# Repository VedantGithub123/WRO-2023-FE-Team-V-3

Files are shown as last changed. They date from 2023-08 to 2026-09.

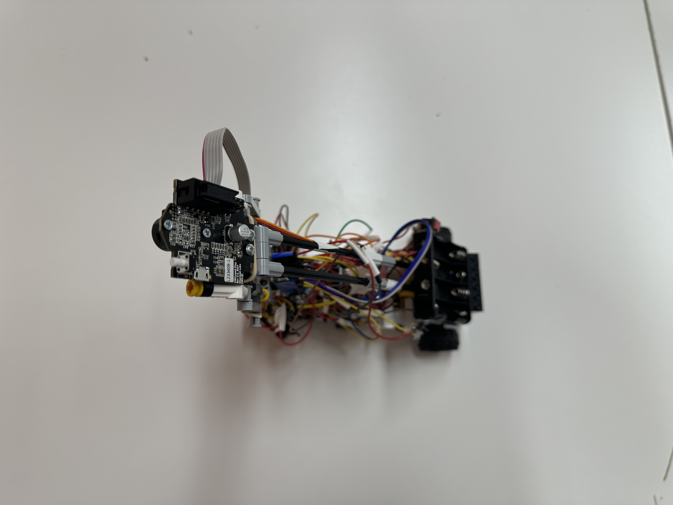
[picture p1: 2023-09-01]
photos/v-photos/v_top.jpg

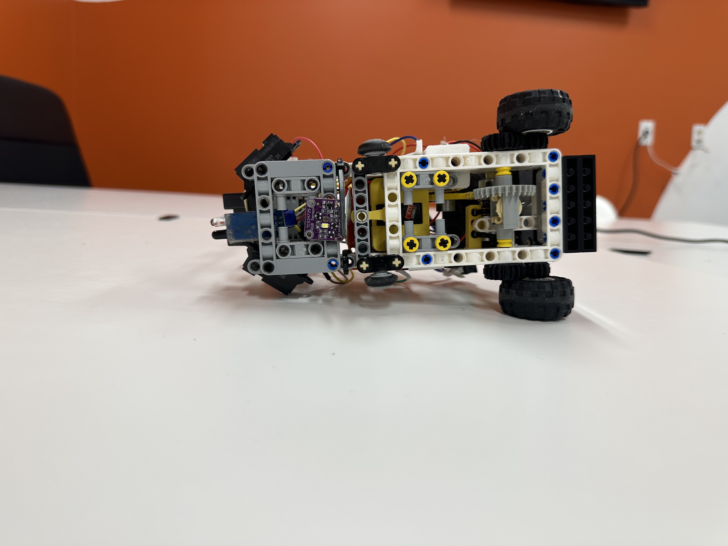
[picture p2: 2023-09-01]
photos/v-photos/v_bottom.jpg

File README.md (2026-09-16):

WRO Future Engineers Team V^3 Engineering Documentation
====

This repository contains engineering materials of a self-driven vehicle model participating in the WRO Future Engineers competition in the 2023 season. More information on each subcomponent of the robot is placed in the README.md files in each folder.

## Content
* `build` contains documentation about our chassis and material choice
* `electrical` contains schematic diagrams demonstrating the connections between different electromechanical components. It also includes the available datasheets for the aforementioned components, and it also has a markdown file explaining the reasoning for each component.
* `models` contains the files used by 3D printers to produce the vehicle elements.
* `photos` contains two folders where one contains the team photos and the other contains the robot photos
* `src` contains the code of control software for all components that were programmed to participate in the competition
* `strategy` contains documentation and diagrams explaining our approach to the problem
* `video` contains the video.md file with the link to a video where the driving demonstration exists

## Rubric Requirements
* `Mobility Management` is found in `build`, `electrical`, and `models`
* `Power and Sense Management` is found in `electrical`
* `Obstacle Management` is found in `strategy` and `src`
* `Pictures - Team and Vehicle` is found in `photos`
* `Performance Videos` is found in `video`
* `Engineering Factor` is found in `build` and `README`

### Who We Are
Team V^3 is an aspiring group of high school and university students who aim to be leaders in the future of autonomous vehicles. By taking the initiative to take part in the WRO Future Engineers challenge, we hope to gain experience in this field of engineering and problem-solving. We have been exposed to many robotic and logical challenges through Zebra Robotics, where we participated in many problems, such as WRO Robomissions, FIRST LEGO League, and VEX Robotics Competition. Our goals for this season are the following:
- Gain knowledge in the field of autonomous vehicles
- Expose ourselves to the nuances of software organization (i.e. Github)
- Become proficient in the skills regarding electronic components
- Learn how to coordinate and work as a team to solve the problem with innovation and creativity

### Our Robot & Iterations
Our team has designed a four-wheel rear-driver autonomous vehicle to complete the 2023 WRO Future Engineers challenge. When making our robot, we wanted to be able to rapidly iterate and make changes whenever they were needed. To accomplish this, our chassis and frame are almost entirely made of LEGO Technic parts and any remaining additions and part adapters (i.e., motor adapters, sensors, etc.) were designed on SolidWorks and Fusion 360 CAD Software and were printed using PLA filament on Anycubic Kobra 3D printers. Our current robot is a small and compact vehicle causing it to be highly maneuverable, allowing us to avoid obstacles effortlessly. This vehicle is powered by 300rpm 6V Micro Gear Box DC motors, allowing us to keep a compact and lightweight robot. To steer this chassis, we are using the ES08MA Metal Analog Servo, which has an ample amount of torque and strength. This allows us to make sharp turns whenever needed.
Prior to making this robot, our team went through various different iterations and prototypes where we learnt many lessons about what our optimal robot should consist of. These lessons are the following:
- Be small and compact
- Effectively use sensors to identify our location and our ideal path
- Speed is not the first priority for this challenges
- Maneuverability is key to solving the obstacle challenge

One of these was a larger robot with the usage of many more sensors and parts. However, its large nature at 30x20x30cm caused it to be difficult to maneuver and control. All of our efforts were in vain as we faced many hardships and problems when trying to program that robot. Our robot’s turning radius was too large, and it was unable to maneuver around the obstacles while our sensors were placed inconveniently and were unable to correctly and quickly construct an efficient path for our robot to take. We realized that many parts of our robot were unnecessary, especially the sheer size of it, and we ultimately decided to do a complete redesign which led to our final robot design. A summary of the reasons for our redesign can be found below:

| | Pros | Cons |
| - | ---| ---|
| Old Robot | <ul><li>Allows for the attachment of larger sensors</li><li>Faster robot due to the larger, more powerful motors</li></ul> | <ul><li>Bad maneuverability due to size, causing a larger turning radius</li><li>Excessive use of unnecessary sensors</li><li>Not enough ports due to the sheer number of sensors</li></ul> |
| New Robot | <ul><li>Smaller and more compact</li><li>Better maneuverability and sharper turning radius</li><li>More effective use of sensors and gets rid of any unnecessary parts</li></ul> | <ul><li>Slower speed due to less powerful motors</li><li>Restrictions to the size of sensors and parts we can use</li></ul> |

| Old Robot | New Robot |
| --- | --- |
|  |  |

### Electrical Components
Our chassis is controlled by the Arduino Nano microcontroller, which gets information from various sensors and uses said information to control the motors using an L298N motor controller board. The sensors that we are using for our vehicle are the following:
- Pixycam 2.1
- TCS34725 RGB Sensor

- HW-201 IR Sensors
- GP2Y0A02YK0F IR Range Sensor
- L3G4200D 3-Axis Gyro

We use the Pixycam 2.1 to identify the locations of the obstacles and effectively avoid them. The TCS34725 RGB sensor tells the microcontroller when it reaches a corner. Both IR sensors are used to detect the walls on the side and on the front. Finally, we use the L3G4200D gyro to know which direction we are facing. More information about our robot’s electrical components can be found in the README file in the electrical folder.

### Strategy and Code
For the open challenge, our sensors are strategically placed in ways that allow us to detect walls at a 45° or less angle. This allows us to adjust accurately based on the distance from the wall, ultimately providing an optimal path to solve this challenge. In order to measure the number of laps we do, we use the RGB sensor to count the number of lines passed and then our robot stops after some time once 12 lines have been measured. This is implemented in the code by using the following lines:
```
if (cornerCount==12)
{
  endTime = millis()+5000;
}
```

The cornerCount variable keeps track of how many corners the robot has passed during its run. The number is twelve as the square-shaped mat has 4 corners, and the robot must complete three laps.
We have two strategies for the obstacle challenge. The first of which only focuses on one block at a time and avoids it. The other strategy involves planning a route for each stretch of the lap and getting the robot to follow that path. Some code for the first challenge is the following:

```
if (closeBlock.m_signature==1)
{
  target = (207-closeBlock.m_y)/1.3-15;
}
else
{
  target = 315.0-(207-closeBlock.m_y)/1.3+15;
}
err = -150.0*(closeBlock.m_x-target);
```

This code gets the closest block and sets the target position of that block onto either side of the robot based on the color of the block.

All in all, this robot is a testament to our team’s adaptability and problem-solving skills, as we were able to completely redesign and program a new and more compact robot after learning from our previous mistakes. We hope that this robot and our hard work will lead us to success, and we look forward to competing!

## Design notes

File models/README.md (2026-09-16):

Models
====

This directory contains all the models used for our robot. Since our robot is made out of LEGO technic pieces, we are going to be 3d printing mounts and adapters for the electronics. Below is a table of our 3D-printed parts and what they are used for.

| File Name | Description | Image |
| --- | --- | --- |
| gear.stl | To solve the problem of transferring the power from the 6V motors to the LEGO axles, we designed and 3D printed a gear that is mounted on the motor's shaft and meshes with the LEGO differential. We had to create our own gear because the motors have a 3mm D-shaped insert which differs from a plus-shaped LEGO axle. |  |
| motor-mount.stl | With motor stability being a crucial part of our drivetrain, we needed to create our own mount to properly secure the motors to our chassis. This helps with our robot's balance and evens out the centre of gravity by allowing us to place one motor on opposite sides. |  |
| motor-bracket.stl | This piece has similar functionality to our motor mounts, except it required a different shape due to where it was placed in our robot. |  |
| servo-adapter.stl | Similar to the motor adapter, our servo motor's power must also be transferred to LEGO pieces. As a result, we created a matching axle slot, which we tuned by prototyping with different dimensions, and a slot for the servo motor, which we also adjusted by creating multiple iterations. |  |
| servo-mount.stl | Our servo motor needed to be secure in order to have crisp steering and minimal unwanted movement. To achieve this, we modelled a mount for the servo motor that would attach to our chassis and also contain a slot that perfectly fits the servo motor. |  |

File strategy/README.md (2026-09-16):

Strategy
====

This directory consists of an explanation and diagrams of our strategy for both the open and obstacle rounds.

## Open Challenge Strategy

In the open challenge, the only changes to the field are the size of the interior walls. In order to combat these changes, we will be using IR distance sensors to identify the distance from the walls. By having multiple distance sensors, the robot can accurately calculate the distance to the surrounding walls. The robot can use these sensor readings to correct itself and make sure it goes parallel to the wall. The robot will know when to turn due to the usage of a RGB sensor which detects the colored lines in the corner. This will also allow us to keep track of the number of laps we complete so we know when to end. Below are diagrams and flow charts demonstrating the process.
| Straight Movement | Turning |
| --- | --- |
|  |  |

| Open Challenge Flowchart |
| ------------------------ |
|  |

## Obstacle Challenge Strategy

For the obstacle challenge, we have two strategies for approaching the problem. The first one is to only consider the first obstacle and act according to that, while the other is to plan a path for one side of the round and follow that. We are working with both strategies and testing both simultaneously to determine the better strategy. To detect the obstacles, we are using the Pixycam 2.1, which gives a list of objects to the Arduino Nano.

### Strategy 1

The first strategy to approach the obstacle challenge is to keep the closest color on the corresponding side of the robot. This is implemented by getting the x-position of the object on the camera and accordingly changing the steering to make sure the object is on the correct side. The turning and stopping will use the same logic as the open challenge. In order to know how much to steer when we see the object, we will use a proportional control loop to ensure that our movements are efficient.

| Obstacle Challenge Simple Approach |
| ---------------------------------- |
|  |

### Strategy 2

Our second strategy for the obstacle challenge is to plan a path for each stretch of the mat and get the robot to follow that path. By having the current position, current heading, target position, and target heading, we can generate a polynomial to fit these parameters. We do this with multiple target points to create a target path which we aim to follow and steer the robot so it aims to move in the direction of the next point. This path takes into account the position of the obstacles and maps points that avoid them. We then repeat this process until the three rounds are over. 

| Obstacle Challenge Complicated Approach |
| ---------------------------------- |
|  |

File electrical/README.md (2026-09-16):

Electrical
====

This directory consists of schematic diagrams demonstrating the connections between different components as well as datasheets for the components. It also consists of the reasoning behind the choice of components.

## Parts Explanation

| Part Name | Explanation | Image | Datasheet |
| --- | --- | --- | --- |
| 1.5V Rechargeable Lithium Ion Battery | We are using this battery to power all of our electronics as it is compact and easy to get. They are also efficient for us as they are rechargeable and do not have to be replaced. |  |  |
| DC 6V Micro Gear Box Speed Reduction Motor, 300RPM | We are using this specific motor to drive the robot as it contains a gearbox that can reach a maximum speed of 300RPM. The compact size of these motors, coupled with a high RPM, allowed for our smaller compact design to succeed. |  |  |
| CJMCU34725 TCS34725 RGB Light Color Sensor | Using this RGB color sensor allows our robot to sense the blue and orange lines at the corners of the mat. This allows us to keep track of how many laps the robot has completed and indicate when the robot needs to turn. |  | [Color Sensor Info](https://www.waveshare.com/w/upload/b/bb/TCS34725_Color_Sensor_user_manual_en.pdf) |
| Arduino Nano | In order to process the information from the sensors and make decisions based on the running code, we are using the Arduino Nano, which is programmed with the Arduino IDE. This board is easy to use, and there are many libraries available and on demand. The board contains 14 digital input/output pins, enabling us to connect a multitude of devices. It also has eight analog pins, of which two are used for I2C communication. |  | [Arduino Nano Info](https://www.arduino.cc/en/uploads/Main/ArduinoNanoManual23.pdf) |
| ES08MA Metal Analog Servo | In order to steer our vehicle, we use a servo motor with 2.0 Kilogram-force centimetres of torque and a speed of 0.10 sec/60°. Since steering will require a reasonably large amount of torque, this motor provides more than enough for our application. Furthermore, this servo motor can turn quickly, which allows us to make incredibly sharp turns. |  | [Servo Info](https://m.media-amazon.com/images/I/61ZU3A84tYS._AC_SL1000_.jpg) |
| GP2Y0A02YK0F IR Range Sensor | The IR sensors provide the necessary information on the distance to the walls at an extremely fast rate. These specific sensors sense distance accurately from 20 to 150cm. We use one of these sensors to detect how close we are to any wall in front of our robot. We use the other two to follow the wall to make sure or robot is in the middle of the track |  | [GP2Y0A02YK0F IR Range Sensor Info](https://cdn.robotshop.com/media/d/dem/rb-dem-02/pdf/datasheet-gp2y0a02yk0f.pdf) |
| GP2Y0A41SK0F IR Range Sensor | We use these sensors to measure the distance to any walls on the sides of our robot. Since we need sensors with a smaller range to detect when we are getting close to the wall, we are using these ones. |  | [GP2Y0A41SK0F IR Sensor Info](https://www.pololu.com/file/0J713/GP2Y0A41SK0F.pdf) |
| HW-201 IR Sensor | In order to detect if our robot is going to crash into any object in the front, we use these sensors as a fail-safe to make sure our robot will still work. |  | [HW-201 IR Sensor Info](https://www.circuits-diy.com/hw201-infrared-ir-sensor-module/) |
| L298N Dual H-Bridge Motor Driver | To effectively power our motors, we are using the L298N motor driver, where we are able to control the direction and speed of both motors using Pulse Width Modulation (PWM). |  | [Motor Driver Info](http://www.handsontec.com/dataspecs/L298N%20Motor%20Driver.pdf) |
| L3G4200D Triple Axis Gyro Angular Velocity Sensor Module | We use a gyro angular velocity sensor to determine our vehicle's angular direction and accurately measure the change in angle per turn. To get accurate angle measurements from the gyro, we integrate the yaw angular velocity after calibrating the gyro to determine the robot's angle relative to its starting position.  |  | [Gyro Info](https://www.elecrow.com/download/L3G4200_AN3393.pdf) |
| PixyCam Pixy 2.1 Robot Vision Image Sensor | Since the Arduino Nano does not have enough computing power to process images, we are outsourcing the processing to the Pixy 2.1. This camera is able to provide the microcontroller with the necessary information to plan an appropriate path for the robot to take. |  | [Pixy 2.1 Info](https://docs.pixycam.com/wiki/doku.php?id=wiki:v2:start) |

## Parts Bill Of Materials (BOM)
| Part Name | Quantity |
| ---| --- |
| 1.5V Rechargeable Lithium Ion Battery | 4 |
| DC 6V Micro Gear Box Speed Reduction Motor, 300RPM | 2 |
| CJMCU34725 TCS34725 RGB Light Color Sensor | 1 |
| Arduino Nano | 1 |
| ES08MA Metal Analog Servo | 1 |
| GP2Y0A02YK0F IR Range Sensor | 3 |
| GP2Y0A41SK0F IR Range Sensor | 2 |
| HW-201 IR Sensor | 1 |
| L298N Dual H-Bridge Motor Driver | 1 |
| L3G4200D Triple Axis Gyro Angular Velocity Sensor Module | 1 |
| PixyCam Pixy 2.1 Robot Vision Image Sensor | 1 |

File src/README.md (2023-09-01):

Control software
====

This directory contains the code required for our robot and explains it

## Software and Language
To program our robot, we use the Arduino IDE and code an Arduino Sketch based on C++. Compiling and uploading our code is a simple process, as there are two buttons to help verify and upload our code. The click of this button will automatically compile and upload our code to the Arduino Nano microcontroller.

## Organization of Code
Our code follows Object-Oriented Programming (OOP) conventions, where we utilize classes for each and every one of our robot's sensors and components. The libraries that we are using to interface with our electronic components are:
Servo.h (For controlling the servo motor)
Adafruit_TCS34725.h (For reading the RGB sensor)
Adafruit_Sensor.h (For reading the gyro sensor)
Wire.h (For reading the gyro sensor)
Pixy2.h (For reading the Pixy camera)
### Chassis Class
In the chassis class, five-member variables are utilized to control the driving motors and the steering. These variables are "enA", which is used to store the pin that is connected to the enable port on the motor controller, and "in1" and "in2", which are used to store the pins connected to the inputs on the motor controller. We also use "sPort," which holds the pin connected to the micro servo. Finally, we have a steering variable, an instance of the steering class imported from the Servo.h library, which is used to control the micro servo we are using.

The constructor for this class takes in four inputs which are the ports used for the chassis, as mentioned above. These inputs are then stored in the member variables for later use in the class instance. 

The first method in our class is the move function which takes in an integer speed and limits it from -255 to 255. It then goes through some logic determining which inputs to turn on or off to drive in the right direction. In the following code, we check if the speed is zero, positive, or negative and set the input pins accordingly.
`if (speed == 0) { digitalWrite(in1, LOW); digitalWrite(in2, LOW); } else if (speed > 0) { digitalWrite(in1, HIGH); digitalWrite(in2, LOW); } else { digitalWrite(in1, LOW); digitalWrite(in2, HIGH); }`

The second method in our class is the steer function which steers our servo motor to the right angle. This method limits an angle variable to a specific range and then writes that range to the servo motor's input pin. The following code limits the range to -70 to 70, adding 94 as an offset.
`steering.write(angle / abs(angle) * min(abs(angle), 70) + 94);`

The third and final method in our class attaches the servo port to the instance of the Servo class defined in the chassis class. This is done by implementing the following code.
`steering.attach(sPort);`

### rgbSensor Class
The rgbSensor class interfaces with the TCS34725 RGB sensor using I2C (Inter-Integrated Circuit) communication to get the RGB values from the sensor. This class has one member variable, the "Adafruit_TCS34725 tcs", which controls the RGB sensor.

The first method in this class is the "getColor" function which returns the detected colour. The following code gets the RGB values and sets the corresponding variable to the values. `tcs.getRGB(&red, &green, &blue);` We then check the blue and red values to determine if the sensor is seeing blue, orange, or white in the following code. `if (blue > 90 && red < 60) { col = 2; } if (red > 80 && blue < 60) { col = 1; }`

The second method in this class is the "setup" function, which starts the TCS34725 sensor.

### IRSensors Class
This class is used to interface with the IR sensors that we are using. The member variables in this class are "int irPorts[4]" which is an array of four ports that hold the ports the sensors are connected to.

The constructor of this class takes in an array as input and assigns the values of the array to the irPorts array.

The first method of the class is the "getDistance" function which returns values based on which sensor it is using. If the sensor is the one in the front used for sensing long distances, we map the voltage to a function that returns the length. This function is implemented in the following code. `return (11.63417 + (241.6444 - 11.63417)/pow((1 + (analogRead(irPorts[port])*5.0/1023.0/0.5075672)), 1.868922))*1.5;` If the sensor is the one in the front and is used for short distances, we return one if it senses something and zero if not. Finally, if none of those are done, we return one if the sensor output voltage is larger than 0.93V and 0 if not.

The second method in this class is the "getDistanceClose" function which acts the same as the "getDistance" function but only returns one for the default case if the voltage is larger than 3.4V.

The third method in this class is the "getFarDistance" function which maps the voltage read from the IR sensor to a function to return the distance seen. This is done with the following code. `return ((138.672)/pow(1.0 + 5.56591*(analogRead(irPorts[port])/200.0), 1.24888)) + (-0.0340614 * pow(analogRead(irPorts[port])/200.0, 3));`

The final function in this class is the setup function which sets the pin modes for all the ports.

### Gyro Class
The Gyro class is used to interface with the L3G4200D gyro sensor through I2C communication. This class has four member variables which are the "angle", "prevTime", "drift", and "L3G4200D_Address".

The first method of the class is the "setup" function which writes to the gyro registers to set it up for use. This is done in the following code. `writeRegister(L3G4200D_Address, CTRL_REG1, 0b00001111); writeRegister(L3G4200D_Address, CTRL_REG2, 0b00000000); writeRegister(L3G4200D_Address, CTRL_REG3, 0b00001000); writeRegister(L3G4200D_Address, CTRL_REG4, 0b00110000); writeRegister(L3G4200D_Address, CTRL_REG5, 0b00000000);`

The second method is the "writeRegister" function which utilizes the "Wire.h" library to write to a particular address.

The third method is the "readRegister" function which also utilizes the "Wire.h" library to read information from a particular address.

The fourth method is the "getGyroChange" function which gets the angular velocity of the gyro. This is done by using the "readRegister" function and shifting the bits to get the value as shown in the following code. ` return ((zMSB << 8) | zLSB);`

The fifth method in the Gyro class is the "getAngle" function which returns the robot's angle by returning the "angle" variable stored in the Gyro class.

The sixth method in the Gyro class is the calibrate function which takes 6000 sample inputs and finds the average. This is the drift of the gyro, which we store in the drift variable for later use. We do the calibration with the following code. `for (int i = 0; i < 6000; i++){ drift +=getGyroChange(); } drift /= 6000; prevTime = micros();`

The final function in the class is the "updateGyro" function which updates the angle of the gyro when called. It does this by multiplying the value of the gyro by the time since the last call and then by a constant and adding that to the angle variable. This is done in the following code. `angle += (micros() - prevTime) / 1000000.0 * (getGyroChange() - drift) / -14.286 * 9/8 * 90/95; prevTime = micros();`

### Camera Class
The Camera class interfaces with the PixyCam 2.1 through SPI (Serial Peripheral Interface) and gets the detected blocks. The member variable in this function is the "pixy" variable, an instance of the Pixy2 class provided by the "Pixy2.h" library. 

The first method in the class is the "setup" function which initializes the PixyCam 2.1. This is done by using the "pixy.init()" function provided in the library.

The second method in the Camera class is the "getClosest" function which returns the closest signature to the robot. The PixyCam 2.1 has the closest signature as the first element in the array of blocks, so we return that first signature as shown in the following code `pixy.ccc.getBlocks(); return pixy.ccc.blocks[0];`

The final method in the class is the "getClosestBlock" function which gets the closest signature which is green or red. This is done to ensure that we do not return the line. We do this by going through the array of blocks, and if the signature is less than or equal to two, we return that block.

## Setup Code
In the setup of our program, we have a multitude of global functions and variables that we use in our main program. 

Arduino requires us to have a `void setup()` function, which runs once when the Arduino is turned on and a `void loop` function, which runs repeatedly until the Arduino turns off. In our code, we keep the setup of all the sensors and then wait until the button is pressed in the `setup` function, and we use the `loop` function to run our code. The first function that we use in our code is the `void delay_2` function which takes in an integer value and delays for that amount of milliseconds while updating the gyro sensor. We use this function instead of the default `delay` function since it allows our gyro sensor to constantly update. We then have two separate functions for each challenge. The `void open` function contains the code for the open challenge, and the `void obstacle` contains the code for the obstacle challenge. We implement these functions in the `loop` function by commenting on which function we are not running and uncommenting the function that we are running.

The global variables that we have in our code are the following
| Variable Name | Type | Purpose |
| --- | ---- | --- |
| chassis | Chassis | Creates an instance of the Chassis class for movement |
| rgbSense | rgbSensor | Creates an instance of the rgbSensor class for sensing lines |
| irPorts | int[4] | Stores the values of the IR sensors' ports |
| irSensors | IRSensors | Creates an instance of the IRSensors class to use the IR sensors |
| gyro | Gyro | Creates an instance of the Gyro class to measure the robot's angle |
| camera | Camera | Creates an instance of the Camera class to detect obstacles |
| buttonPort | int | Stores the port of the button |
| speed | int | Defines the speed for the robot and is used for acceleration |
| cornerCount | int | Stores the number of corners passed |
| endTime | unsigned long int | Stores the time when our robot should stop moving |
| dir | int | Stores the direction of the lap |
| cornerScanDelay | unsigned long int | Stores the time a corner was passed |
| cornerDetected | bool | Stores if a line has been detected |
| steer | float | Stores the steering value |
| prevObj | Block | Stores the previous block |
| closeBlock | Block | Stores the closest block |
| target | int | stores the target position for the blocks |
| err | float | Stores the error for following |
| kP | float | Stores the kP value for following |
| objDelay | int | Stores the time when an object is passed |
| targetAngle | int | Stores the target angle for gyro following |
| caughtOnWall | bool | Used to detect when to wall follow |

## Open Challenge Code
In the open challenge, we implement gyro and IR following, which uses readings from the sensors to ensure a straight path. Before we pass the first corner, the robot does not know which direction it is travelling in, so it gyro follows. We implement gyro following in the following code where it finds the difference between the target angle and the current angle and multiplies that error to get the steering. `err = targetAngle - gyro.getAngle(); steer = err*2.0;` To set our direction, we run this code constantly which checks if the direction is not set, it will reset it to whatever the RGB sensor is seeing. `if (dir==0) { dir = rgbSense.getColor(); }` The next part of our code checks if the RGB sensor sees the same color as the direction that the robot is travelling and it has been 2 seconds since the last line was seen and increments to cornerCount, sets the end time to after 3 seconds, flags the cornerDetected variable as true, changes targetAngle, and resets cornerScanDelay. We do this in the following code. `if (rgbSense.getColor()==dir && dir!=0 && millis()-cornerScanDelay>2000) { delay_2(60); cornerCount++; endTime = millis()+3000; cornerDetected = true; targetAngle += (dir == 1 ? 90 : -90) cornerScanDelay = millis(); }` We then have a code to check if the cornerDetected variable is true, the robot is close to the wall, and the robot is not wall following, and if all the conditions are true, the robot will take a turn based on which direction the robot is travelling. We then check if the robot is close to the walls, and if it is, we set the caughtOnWall variable to true so that the robot will start wall following. We then check if the robot is too close to the walls on the side and turn if so. We then check if we are supposed to wall follow, and wall follow if so. The wall following is done with the following code. `if(caughtOnWall) { if(dir == 1) { err = 20.0 - irSensors.getFarDistance(2); steer = err * -2.0; } else if(dir == 2)  { err = 20.0 - irSensors.getFarDistance(0); steer = err*2.0; } if (steer>15){ steer = 15; }else if (steer<-15){ steer = -15; } }` We then make sure that the steering is not greater than 30 degrees and we set the steering and speed if it is not time to stop the run.

## Obstacle Challenge Code
For the obstacle challenge, we use a variety of sensors, including the RGB sensor, IR sensors, gyro, and camera. Our code uses these sensors to avoid obstacles and turn effectively. This code is split into two main parts. The first part is the normal navigation, and the other part is the turning logic. In the normal navigation logic, we start off by checking if the time since the corner turned is less than 2 seconds and get the closest signature based on that. We then set the prevObj variable to the current block if the block is close enough to the robot in the following code. `if (closeBlock.m_y>150 && closeBlock.m_signature<=2) { prevObj = closeBlock; }` We then have the same direction detection logic as the open challenge. After that, we have the block following which we do if we see a block, not a line or nothing which is done in the following code. `if (closeBlock.m_signature<=2) {  if (closeBlock.m_signature==1) { target = (207-closeBlock.m_y)/1.5 + 5; }else { target = 310.0-(207-closeBlock.m_y)/1.5; } err = target - (int)closeBlock.m_x; steer = err*kP; if (steer>30){ steer = 30; }else if (steer<-30){ steer = -30; } }` If there is no block sensed, we run the wall following code which is done with the following code. `err = 60 - irSensors.getFarDistance(dir == 1 ? 0 : 2); steer = err * (dir == 1 ? 1.0 : -1.0) * 1.0; if (steer>10){ steer = 10; }else if (steer<-10){ steer = -10; }` We then have some code which makes sure we don't crash int anything on the side which is done by using the IR sensors to detect the distance from the sides and turn accordingly. We do this in the following code. `if (irSensors.getFarDistance(0) <= 15) { if(closeBlock.m_signature != 1) { steer = 20; } else if (irSensors.getFarDistance(0) <= 12)  steer = 30; }else if (irSensors.getFarDistance(2) <= 15) { if(closeBlock.m_signature != 2) { steer = -20; } else if (irSensors.getFarDistance(2) <= 12)  steer = -30; }` This code checks the side sensors and the current block that the robot is seeing to determine which direction and how much to turn. After this is done, we have an if statement to identify if our robot is going to crash from the front, and if so, the robot will move backwards for three seconds and resume the program. The last part of normal navigation is where the robot sets the steering and speed if the time is not up. For the turning logic, we have an if statement that checks if it is time to turn and runs the code accordingly. The first thing that happens in the if statement is that we increment to cornerCount and check if we need to set the stopping time. We then check if the last block passed was red, and the robot finished the second lap and ran the 180-degree turn where the robot uses the gyro to go close to the wall and turn. The gyro following is done in this code: `while (irSensors.getDistance(1)>50){ err = targetAngle + 170 - gyro.getAngle(); steer = err*2.0; if (steer>20){ steer = 20; }else if (steer<-20){ steer = -20; } delay_2(1); chassis.steer(steer); gyro.updateGyro(); }` and the turning amount changes based on the direction we are travelling in. If we are supposed to run a normal turn, we check if we need to turn on the outside, inside, or neither and run based on that. For all of these turning cases, we use the gyro sensor to turn. To determine which case to go into, the robot takes eight frames from the camera and checks if a block appears in at least 2 of those frames and based on the block's color, we determine which case to go into.

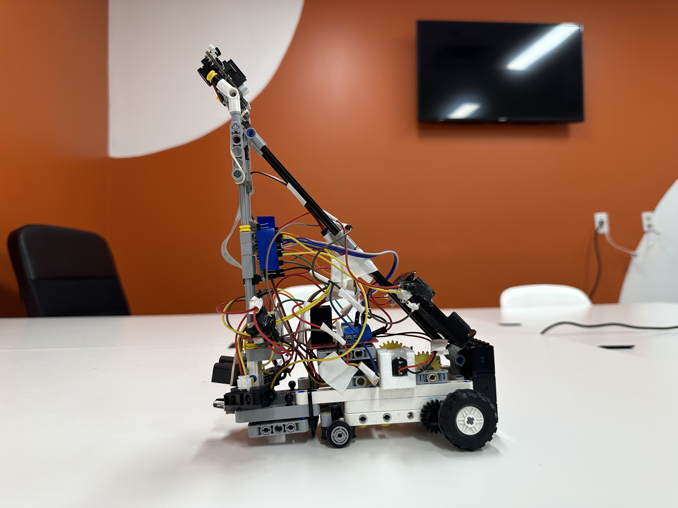
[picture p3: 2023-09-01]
photos/v-photos/v_left.jpg

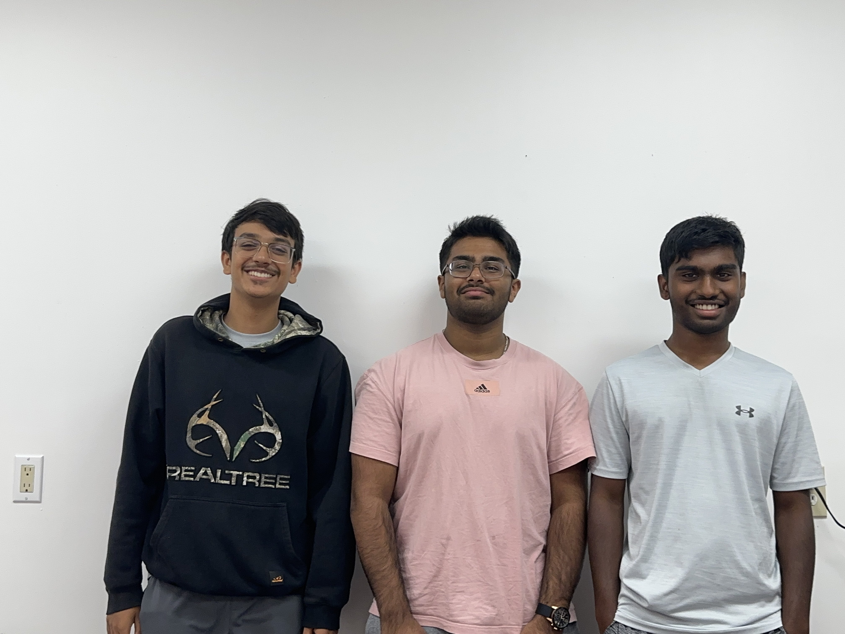
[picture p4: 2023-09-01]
photos/t-photos/t_normal.jpg

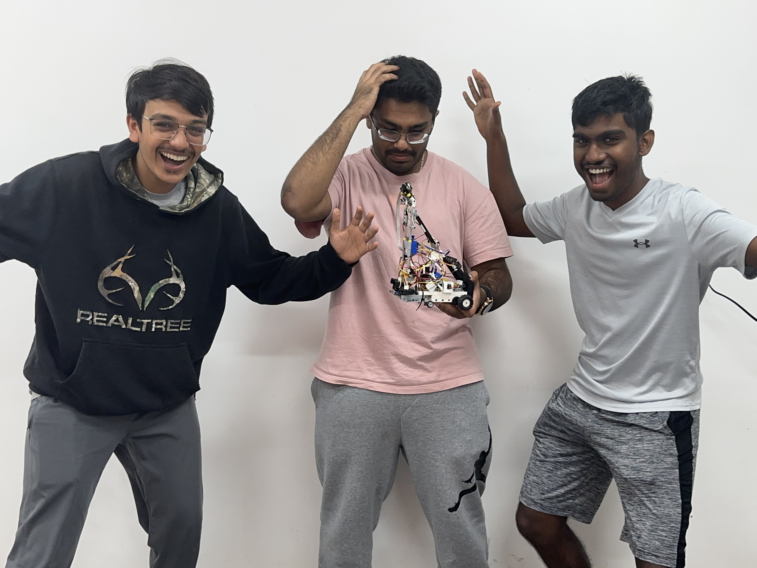
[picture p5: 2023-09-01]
photos/t-photos/t_funny.jpg

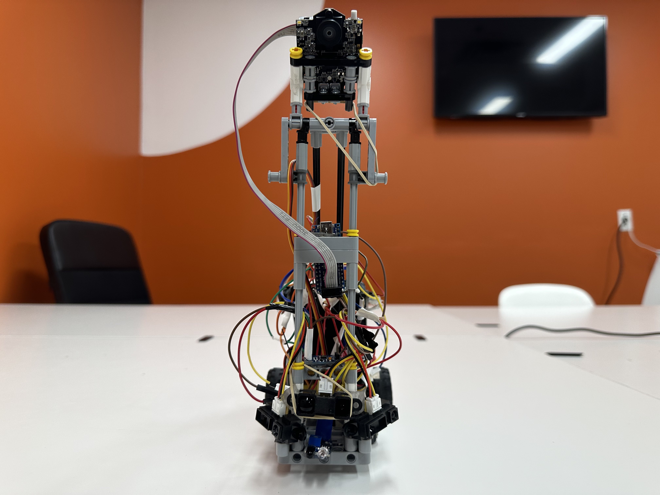
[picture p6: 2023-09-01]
photos/v-photos/v_front.jpg

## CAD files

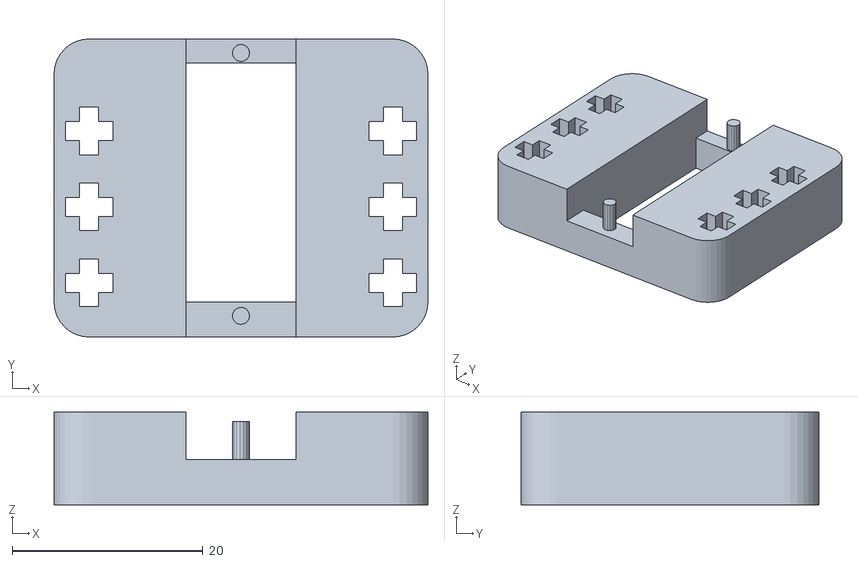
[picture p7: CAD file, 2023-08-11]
models/servo_mount.stl
39.3 x 31.3 x 9.76

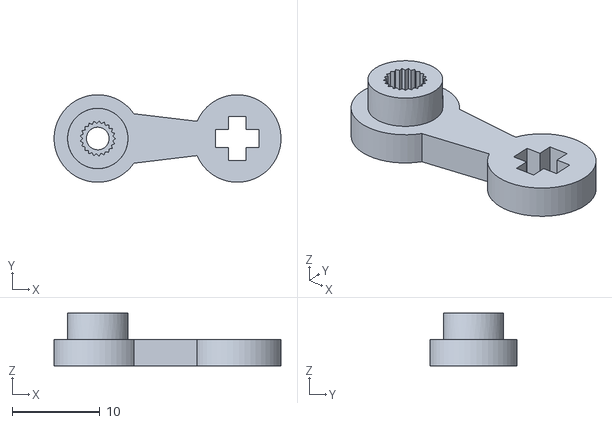
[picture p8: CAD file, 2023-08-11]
models/servo_adapter.stl
25.9 x 9.99 x 6.00

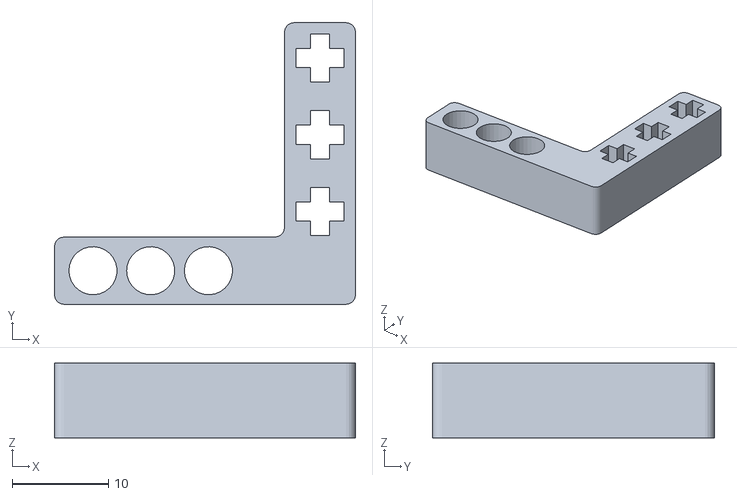
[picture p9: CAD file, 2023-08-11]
models/motor_bracket.stl
31.3 x 29.3 x 7.76

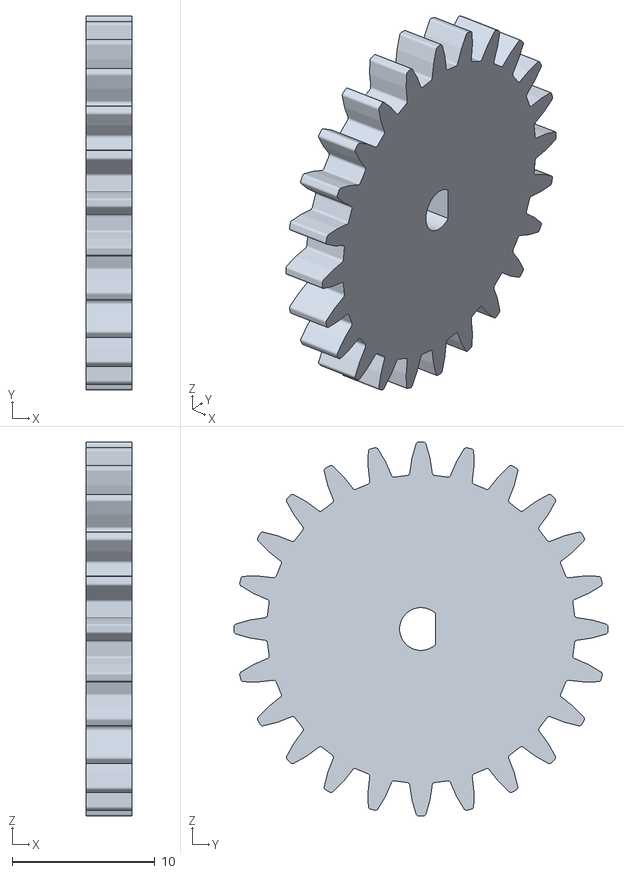
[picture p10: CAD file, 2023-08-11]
models/gear.stl
3.20 x 26.2 x 26.2

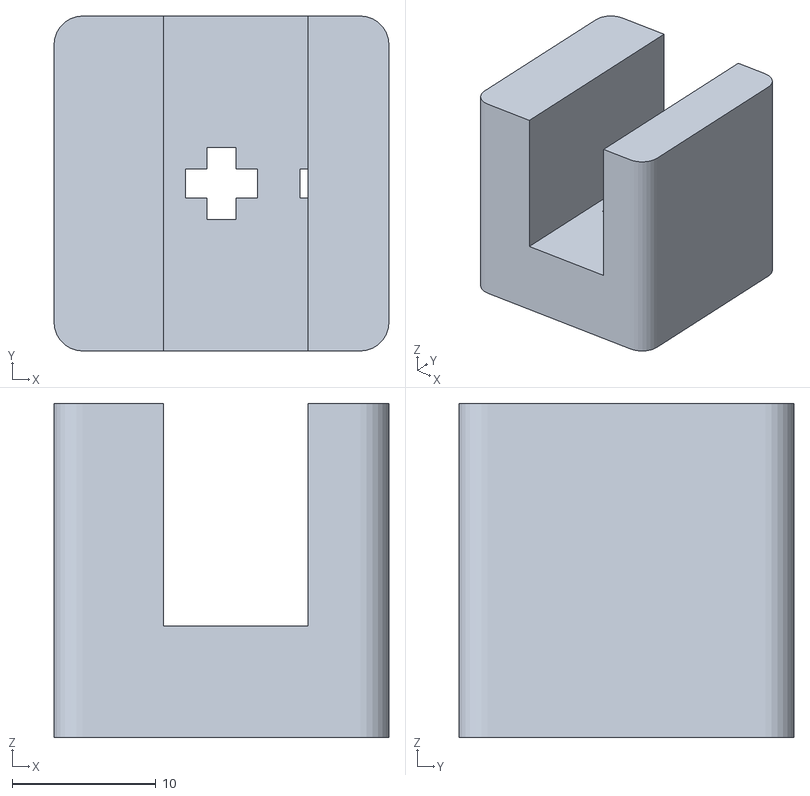
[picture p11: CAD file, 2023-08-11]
models/motor_mount.stl
23.3 x 23.3 x 23.3

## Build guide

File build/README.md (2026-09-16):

Build
====

This directory consists of the different materials used to construct our robot, along with the reasoning for choosing our drivetrain. Attached is a pdf which includes the building instructions as well as a LDraw file of our robot. Our team created this model and instruction to allow easy replication of our robot if needed.

## Chassis Type & Explanation

Our robot is a four-wheeled vehicle which has a rear-wheel drive with steering in the front. We decided to implement a simple chassis since that would reduce the amount of complexity, and therefore chances of failure. In order to keep the drivetrain simple and efficient, we made sure not to have the steering mechanism on the same set of wheels as the driving wheels. This solves the problem of spacing, as the steering motor and the drive motors do not have to be on the same set of wheels. Our decision to do this meant that we could only have two options for driving which were front-wheel drive with steering in the back or a rear-wheel drive with steering in the front. We ultimately chose a drivetrain that had real-wheel drive with front-wheel steering as that made the robot more familiar to use, given our experience using other rear-wheel driven LEGO robots.

| Rear-Wheel Drive | Front Wheel Drive |
| --- | --- |
|  |  |

## Steering

Our steering mechanism is a four-bar with free-spinning wheels mounted on it. The motor will move the four-bar, which changes the angle of the wheels, which in turn changes the direction that the vehicle is travelling in. This type of steering proved to be the most efficient for our purposes and was also the easiest version for us to implement, as it only required a servo motor and a simple rig that connected the servo to the wheel axles. The rig was 3D printed along with the servo mount as one piece and had a LEGO axle-shaped cross hole that would turn along with the servo.

| Four-Bar Steering Mechanism |
| --------------------------- |
|  |

## Materials

When creating our robot, we wanted to be able to easily iterate and update the robot in many ways as we tested it. In order to achieve these goals, we decided to use LEGO Technic pieces to construct the majority of our robot. LEGO technic was the perfect choice for us since our robotics centre, Zebra Robotics, focuses on LEGO robotics and competitions related to that, so we have an abundance of LEGO technic pieces. Our team members also have extensive experience in working with LEGO Technic parts and completing challenges with them. In order to attach the electronic components onto our chassis, we 3D printed mounts for the components, as they allowed us to smoothly integrate the non-LEGO parts with the LEGO parts.

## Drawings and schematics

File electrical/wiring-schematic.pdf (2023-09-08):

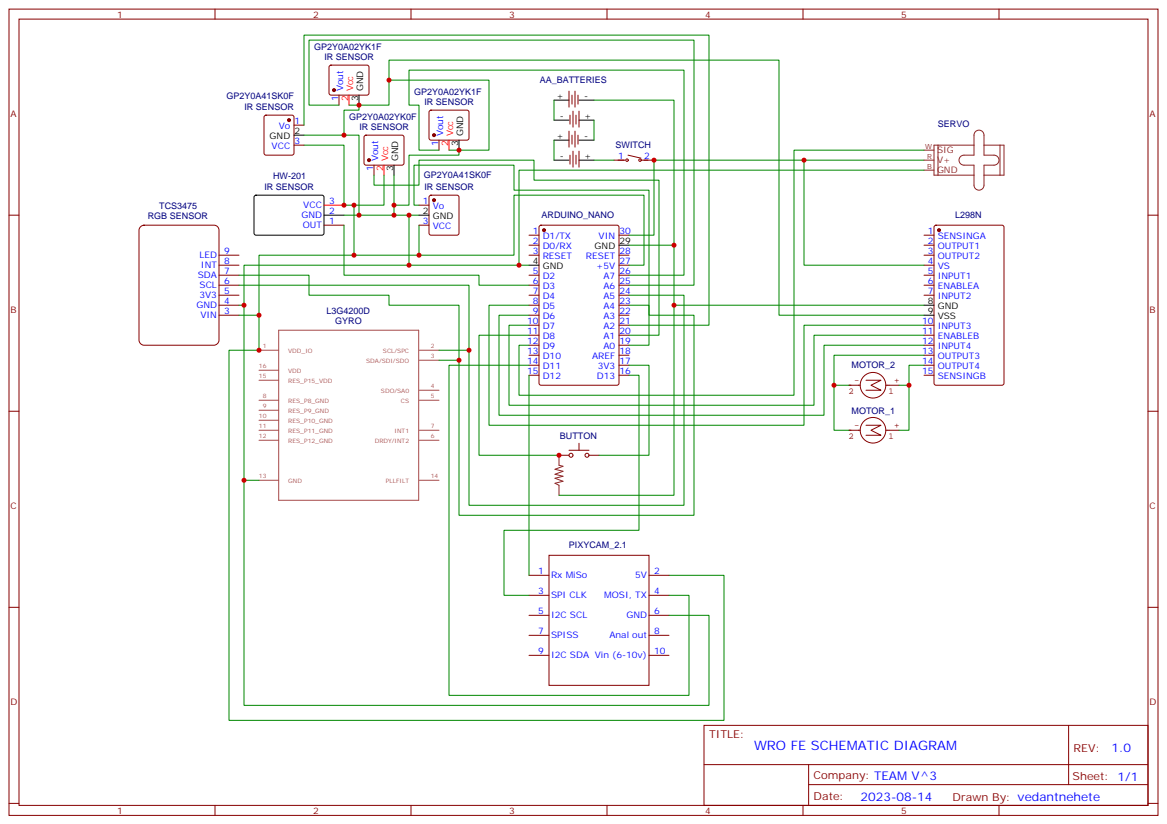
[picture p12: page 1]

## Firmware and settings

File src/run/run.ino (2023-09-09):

// Imports libraries used
#include <Servo.h>
#include "Adafruit_TCS34725.h"
#include <Adafruit_Sensor.h>
#include <Wire.h>
#include <Pixy2.h>

// Defines registries for the gyro sensor
#define CTRL_REG1 0x20
#define CTRL_REG2 0x21
#define CTRL_REG3 0x22
#define CTRL_REG4 0x23
#define CTRL_REG5 0x24


// Creates the Chassis class which includes steering and driving
class Chassis {
public:
  Chassis(int e1, int i1, int i2, int steerPort) {
    enA = e1;
    in1 = i1;
    in2 = i2;

    sPort = steerPort;

    pinMode(enA, OUTPUT);
    pinMode(in1, OUTPUT);
    pinMode(in2, OUTPUT);
  }
  void move(int speed) {
    speed = speed / abs(speed) * min(255, abs(speed));
    analogWrite(enA, abs(speed));
    if (speed == 0) {
      digitalWrite(in1, LOW);
      digitalWrite(in2, LOW);
    } else if (speed > 0) {
      digitalWrite(in1, HIGH);
      digitalWrite(in2, LOW);
    } else {
      digitalWrite(in1, LOW);
      digitalWrite(in2, HIGH);
    }
  }
  void steer(int angle) {
    steering.write(angle / abs(angle) * min(abs(angle), 70) + 94);
  }
  void attachServo() {
    steering.attach(sPort);
  }
  Servo steering;

  int enA;
  int in1;
  int in2;
  int sPort;
};

// Creates the rgbSensor class which is used for the rgb sensor
class rgbSensor {
public:
  int getColor() {
    float red, green, blue;

    tcs.setInterrupt(false);

    tcs.getRGB(&red, &green, &blue);

    tcs.setInterrupt(true);

    int col = 0;  //0: White, 1: Orange, 2: Blue
    if (blue > 90 && red < 60) { col = 2; }
    if (red > 80 && blue < 60) { col = 1; }
    return col;
  }

  void setup() {
    tcs.begin();
  }

  Adafruit_TCS34725 tcs = Adafruit_TCS34725(TCS34725_INTEGRATIONTIME_2_4MS, TCS34725_GAIN_4X);
};

// Creates the IRSensors class which is used to read the IR sensor values
class IRSensors {
public:
  IRSensors(int ports[]) {
    for (int i = 0; i < 6; i++) {
      irPorts[i] = ports[i];
    }
  }

  int getDistance(int port) {
    port = max(min(port, 3), 0);
    if (irPorts[port] == A1) {
      return (11.63417 + (241.6444 - 11.63417) / pow((1 + (analogRead(irPorts[port]) * 5.0 / 1023.0 / 0.5075672)), 1.868922)) * 1.5;
    } else if (port == 3) {
      return 1 - digitalRead(port);
    }
    return analogRead(irPorts[port]) > 200;
  }

  int getDistanceClose(int port) {
    port = max(min(port, 3), 0);
    if (irPorts[port] == A1) {
      return (11.63417 + (241.6444 - 11.63417) / pow((1 + (analogRead(irPorts[port]) * 5.0 / 1023.0 / 0.5075672)), 1.868922)) * 1.5;
    } else if (port == 3) {
      return 1 - digitalRead(port);
    }
    return analogRead(irPorts[port]) > 700;
  }

  float getFarDistanceValue(int port){
    float val = analogRead(irPorts[port]);
    // return -0.131336* + 82.3502;
    return 0.000571671*val*val + -0.496573*val + 130.376;
  }

  float getFarDistanceValue(int port){
    float val = analogRead(irPorts[port]);
    // return -0.131336* + 82.3502;
    return 0.000571671*val*val + -0.496573*val + 130.376;
  }

  float getFarDistance(int port) {
    int sum = 0;
    for(int i = 0; i < 5; i++)
    {
      sum += analogRead(irPorts[port]);
    }
    float x = sum / 5.0;
    return (138.672) / pow(1.0 + 5.56591 * (x / 200.0), 1.24888) + (-0.0340614 * pow(x / 200.0, 3));

    // float max = 0;
    // int val = 0;
    // int x = 0;

    // for (int i = 0; i<1; i++){
    //   x = analogRead(irPorts[port]);
    //   val = (138.672)/pow(1.0 + 5.56591*(x/200.0), 1.24888) + (-0.0340614 * pow(x/200.0, 3));
    //   if (val>max){
    //     max = val;
    //   }
    // }
    // return max;
  }

  float getRawValue(int port) {
    return analogRead(irPorts[port]);
  }

  void setup() {
    for (int i : irPorts) {
      if (i < 14) {
        pinMode(i, INPUT);
      }
    }
  }
  int irPorts[6];
  int irPorts[6];
};

// Creates the Gyro class which is used to measure our heading
class Gyro {
public:

  void setup() {
    writeRegister(L3G4200D_Address, CTRL_REG1, 0b00001111);
    writeRegister(L3G4200D_Address, CTRL_REG2, 0b00000000);
    writeRegister(L3G4200D_Address, CTRL_REG3, 0b00000000);
    // writeRegister(L3G4200D_Address, CTRL_REG4, 0b00110000);
    writeRegister(L3G4200D_Address, CTRL_REG4, 0b00010000);
    writeRegister(L3G4200D_Address, CTRL_REG4, 0b00010000);
    writeRegister(L3G4200D_Address, CTRL_REG5, 0b00000000);
    delay(1);
  }

  void writeRegister(int deviceAddress, byte address, byte val) {
    Wire.beginTransmission(deviceAddress);
    Wire.write(address);
    Wire.write(val);
    Wire.endTransmission();
  }

  int readRegister(int deviceAddress, byte address) {
    int v;
    Wire.beginTransmission(deviceAddress);
    Wire.write(address);
    Wire.endTransmission();
    Wire.requestFrom(deviceAddress, 1);
    delayMicroseconds(1);
    v = Wire.read();
    return v;
  }

  float getGyroChange() {
    byte zMSB = readRegister(L3G4200D_Address, 0x2D);
    byte zLSB = readRegister(L3G4200D_Address, 0x2C);
    return ((zMSB << 8) | zLSB);
  }

  float getAngle() {
    return angle;
  }

  void calibrate() {
    for (int i = 0; i < 6000; i++) {
      drift += getGyroChange();
    }
    drift /= 6000;
    prevTime = micros();
  }

  void updateGyro() {
    angle += (micros() - prevTime) / 1000000.0 * (getGyroChange() - drift) * -1.0 * 0.0186886096*375.0/360.0*720.0/715.0*370.0/360.0*900.0/930.0; // -90.0/9800.0 * 720.0/672.3; // 1440.0/1460.0 * 1440.0/1412.0;
    prevTime = micros();
    Serial.println(getAngle());
  }

  float angle = -4;
  unsigned long int prevTime = micros();
  float drift = 0;
  int L3G4200D_Address = 105;
};

// Creates the Camera class which is used to get certain blocks from the PixyCam 2.1
class Camera {
public:
  void setup() {
    pixy.init();
  }

  Block getClosest() {
    pixy.ccc.getBlocks();
    return pixy.ccc.blocks[0];
  }

  Block getClosestBlock() {
    int numBlocks = pixy.ccc.getBlocks();
    for (int i = 0; i < numBlocks; i++) {
      if (pixy.ccc.blocks[i].m_signature <= 2) {
        return pixy.ccc.blocks[i];
      }
    }
    return pixy.ccc.blocks[0];
  }

  Pixy2 pixy;
};


// Constructs an instance of the classes
Chassis chassis(5, 6, 7, 9);               // For movement
rgbSensor rgbSense;                        // For sensing lines on the mat
const int irPorts[6] = { A0, A1, A2, 3, A6, A7 };  // Ports for the IR sensors
IRSensors irSensors(irPorts);              // For detecting distance in the front and sides
Gyro gyro;                                 // For detecting the angle of our robot
Camera camera;                             // For getting the obstacles
const int buttonPort = 8;                  // Pin for the pushbutton

void delay_2(int s) {  // Function to update the gyro while delaying
  unsigned long int x = millis();
  while (millis() - x < s) {
    gyro.updateGyro();
  }
}

int speed = 0;                            // Defines the speed for the robot
int cornerCount = 0;                      // Number of corners passed
unsigned long int endTime = 10000000000;  // Stores the time when our robot should stop moving
int dir = 0;                              // Stores the direction of our robot: | 0: Undecided | 1: Clockwise | 2: Counterclockwise |
unsigned long int cornerScanDelay = 0;    // Stores time of last line detected for time between corners
bool cornerDetected = false;              // Boolean to store if the line has been detected
float steer = 0.0;                        // Stores the steering
Block prevObj;                            // Stores the last passed block
Block closeBlock;                         // Stores the closest block to the robot
int target = 0;                           // Stores the target position of the blocks
float err = 0;                            // Stores the error for following the object
const float kP = -0.35;                   // Stores the kP for following the object
int targetAngle = 0;                      // Angle to turn gyro
bool caughtOnWall = false;                // Stores if the robot is wall following
int curColor = 0;

void setup() {
  Serial.begin(9600);  // Starts the serial monitor for debugging

  // Sets the pin mode for the button
  pinMode(buttonPort, INPUT);
  // Sets up the electronic components
  Serial.println("ABC");
  chassis.attachServo();
  chassis.steer(60);
  delay(500);
  rgbSense.setup();
  irSensors.setup();
  gyro.setup();
  gyro.calibrate();
  camera.setup();
  chassis.steer(0);  // Aligns steering when everything is ready

  // Start the program once the button is pressed
  int max = 0;
  while (!digitalRead(buttonPort)) {
    delay_2(10);
    // Serial.println(irSensors.getFarDistance(2));
    // Serial.println(irSensors.getFarDistanceValue(4));
    // delay(100);
  }
}

void open() {
  steer = -1;
  speed = 255;

  if (dir == 0) {  // Rewrites direction to the color of the sensor if the direction is not defined
    dir = rgbSense.getColor();
  }

  if (rgbSense.getColor() == dir && dir != 0 && millis() - cornerScanDelay > 2000) {  // Checks if the line is seen and if the time after the last scan was greater than 2000ms
    delay_2(60);
    cornerCount++;            // Increases the amount of corners we have passed
    if (cornerCount == 12) {  // If the gyro angle says 3 laps are finished, stop the robot after some time
      endTime = millis() + 3000;
    }

    cornerDetected = true;  // Flags the cornerDetected variable as true
    targetAngle += (dir == 1 ? 90 : -90);

    cornerScanDelay = millis();  // Updates cornerScanDelay with the current time
  }

  if (cornerDetected && irSensors.getDistance(1) < 40 && !caughtOnWall) {  // Starts turning when the corner is detected and the robot is close to the wall
    // Turns and sets the bias based on which direction the robot is moving
    if (dir == 1) {
      chassis.steer(30);
    } else {
      chassis.steer(-30);
    }

    // Waits until gyro reaches target angle
    while (abs(gyro.getAngle()) < (abs(targetAngle) - 25)) {
      gyro.updateGyro();
    }
    cornerDetected = false;      // Resets cornerDetected variable until the line is seen again
    cornerScanDelay = millis();  // Updates cornerScanDelay with the current time
  }
  err = targetAngle - gyro.getAngle();
  steer = err * 2.0;

  delay_2(1);  //For the gyro
  if (cornerCount >= 1 && millis() - cornerScanDelay > 3000 && !caughtOnWall) {
    if (dir == 1 && irSensors.getFarDistance(2) < 25) {
      caughtOnWall = true;
    } else if (dir == 2 && irSensors.getFarDistance(0) < 25) {
      caughtOnWall = true;
    }
  }

  if (irSensors.getDistance(0)) {
    steer = 30;
  } else if (irSensors.getDistance(2)) {
    steer = -30;
  }

  if (caughtOnWall) {
    if (dir == 1) {
      err = 20.0 - irSensors.getFarDistance(2);
      steer = err * -1.5;
    } else if (dir == 2) {
      err = 20.0 - irSensors.getFarDistance(0);
      steer = err * 1.5;
    }
    if (steer > 15) {
      steer = 15;
    } else if (steer < -15) {
      steer = -15;
    }
  }

  if (steer > 30) {
    steer = 30;
  } else if (steer < -30) {
    steer = -30;
  }

  if (millis() < endTime) {  // If the time is not finished, keep moving the robot
    chassis.steer(steer);
    chassis.move(speed);
  } else {  // If the time is up, stop the robot
    chassis.move(0);
    chassis.steer(0);
    delay(100000000);
  }
}

void gyroTest()
{
  speed = 255;  // Sets speed to 255

  steer = -3;  // Steering is set to straight

  curColor = rgbSense.getColor();

  if (dir == 0) {  // Rewrites direction to the color of the sensor if the direction is not defined
    dir = curColor;
  }

  if (curColor == dir && dir > 0 && millis() - cornerScanDelay > 2000) { 
    targetAngle += (dir == 1 ? 90 : -90);
    chassis.steer((1.5 - dir) * 70);
        while (abs(gyro.getAngle()) < (abs(targetAngle) + 0)) {
      // if(irSensors.getFarDistance((dir == 1 ? 2: 0)) <= 12) break;
      gyro.updateGyro();
    }

  }

      err = targetAngle - gyro.getAngle();
      steer = err*2.0-3;
    
    if (steer>20){
      steer = 20;
    }else if (steer<-20){
      steer = -20;
    }

      chassis.steer(steer);
    chassis.move(255);
    gyro.updateGyro();
}

void obstacle() {

  speed = 255;  // Sets speed to 255

  steer = -3;  // Steering is set to straight

  curColor = rgbSense.getColor();

  if (millis() - cornerScanDelay < 2000)  // right after turning look for block and ignore lines
  {
    closeBlock = camera.getClosestBlock();  // Gets closest block or line from the camera
  } else {
    closeBlock = camera.getClosestBlock();  // Gets closest block from the camera
    gyro.updateGyro();
    if (closeBlock.m_signature != prevObj.m_signature)  // If the current closest block matches the prev block ignore the line logic
    {
      closeBlock = camera.getClosest();  // Gets closest block or line from the camera
    }
  }
  if (closeBlock.m_signature <= 2) {
    if (closeBlock.m_y > 150 && closeBlock.m_signature <= 2) {  // Set the most recent block to the old block
      prevObj = closeBlock;
    }
  }

  if (dir == 0) {  // Rewrites direction to the color of the sensor if the direction is not defined
    dir = curColor;
  }

  if (closeBlock.m_signature <= 2) {
    if (closeBlock.m_signature == 1) {  // Sets the target for the block position on the left based on how far it is if it is red
      target = (207 - closeBlock.m_y) / 1.5 + 5;
    } else {  // Sets the target for the block position on the right based on how far it is if it is green
      target = 310.0 - (207 - closeBlock.m_y) / 1.5;
    }
    err = target - (int)closeBlock.m_x;  // Sets the error to the difference between the current position and the target
    steer = err * kP;                    // Gets steering value
    if (steer > 30) {
      steer = 30;
    } else if (steer < -30) {
      steer = -30;
    }
  } else {
    // If there is nothing to see follow on outside wall
    err = (dir == 1 ? 60 : 70) - irSensors.getFarDistanceValue(dir == 1 ? 4 : 5);
    steer = err * (dir == 1 ? 1.0 : -1.0) * 0.3 + (targetAngle - gyro.getAngle()) * 1.0 - 3; 
    
    if (steer>20){
      steer = 20;
    }else if (steer<-20){
      steer = -20;
    }
  }

  if (curColor == dir && dir > 0 && millis() - cornerScanDelay > 2000) {  // Checks if the color is the same is the direction to travel and if it has been 1 second past the start or the reversing of the 3rd lap
  if (curColor == dir && dir > 0 && millis() - cornerScanDelay > 2000) {  // Checks if the color is the same is the direction to travel and if it has been 1 second past the start or the reversing of the 3rd lap
    cornerCount++;                                                        // Increments 1 to cornerCount
    if (cornerCount >= 12) {                                              // If all the corners are passed, set the program to stop after 3.8 seconds
      endTime = millis() + 3500;
    }
    if (cornerCount == 8 && prevObj.m_signature == 1) {  // If 2 laps are finished and the last object was red, run the turning sequence
      targetAngle -= 180;
      dir = 3 - dir;  // sets the direction to the opposite way
      unsigned long int prevTime = millis();
      chassis.move(0);
      delay_2(3000);
      chassis.move(255);
      while (irSensors.getDistance(1) > 50 || millis() - prevTime < 1000) {
        err = targetAngle + (dir == 2 ? 180 : 180) - gyro.getAngle();
        err = targetAngle + (dir == 2 ? 180 : 180) - gyro.getAngle();
        steer = err * 2.0;
        if (steer > 20) {
          steer = 20;
        } else if (steer < -20) {
          steer = -20;
        }
        if (irSensors.getFarDistance(0) <= 25) {
          steer = 30;
        } else if (irSensors.getFarDistance(2) <= 25) {
          steer = -30;
        }
        chassis.steer(steer);
        gyro.updateGyro();
      }  // Get close to the front wall
      // Turn for gyro
      chassis.steer(-40);
      if (dir == 1) {
        while (abs(gyro.getAngle()) < abs(targetAngle) + 0) {  // Underturn on blue direction
          gyro.updateGyro();
          if (irSensors.getDistance(3)) {
            chassis.steer(0);
            chassis.move(-255);
            delay_2(2000);
            chassis.move(255);
            chassis.steer(-35);
          }
        }
        gyro.angle -= targetAngle-20;
        targetAngle = 0;
      } else {
        while (abs(gyro.getAngle()) > abs(targetAngle) + 30) {  // Underturn on orange direction
          gyro.updateGyro();
          if (irSensors.getDistance(3)) {
            chassis.steer(0);
            chassis.move(-255);
            delay_2(2000);
            chassis.move(255);
            chassis.steer(-35);
          }
        }
        gyro.angle -= targetAngle;
        targetAngle = 0;
      }
      chassis.move(0);
      delay_2(2500);
      chassis.move(255);
      delay_2(1);
      cornerCount++;
    } else {
      int check = 0;
      int check2 = 0;
      for (int i = 0; i < 8; i++) {
        int blockSignature = camera.getClosestBlock().m_signature;
        if (blockSignature == 3 - dir) {
          check++;
        } else if (blockSignature == dir) {
          check2++;
        }
        gyro.updateGyro();
      }
      int originalAngle = targetAngle;
      targetAngle += (dir == 1 ? 90 : -90);
      if (check > 1) {  // If the block in front says that you need to go from the outside of the lap, run the following code
        unsigned long int prevTime = millis();
        while ((irSensors.getDistance(1) > 40 || millis() - prevTime < 1000) && millis() - prevTime < 3500) {  // Follow the block until the robot is close to the wall

          closeBlock = camera.getClosestBlock();
          if (closeBlock.m_signature <= 2) {
            if (closeBlock.m_signature == 1) {  // Sets the target for the block position on the left based on how far it is if it is red
              target = (207 - closeBlock.m_y) / 2 + 5;
              target = 0;
            } else {  // Sets the target for the block position on the right based on how far it is if it is green
              target = 300.0 - (207 - closeBlock.m_y) / 2;
            }
            err = target - (int)closeBlock.m_x;  // Sets the error to the difference between the current position and the target
            steer = err * kP;                    // Gets steering value
            if (steer > 30) {
              steer = 30;
            } else if (steer < -30) {
              steer = -30;
            }
            if (closeBlock.m_signature <= 2) {
              prevObj = closeBlock;
            }
          } else {
            steer = (dir == 1 ? 8 : -8);
          }
          chassis.steer(steer);
          gyro.updateGyro();
        }
        // Turn until the robot sees nothing
        chassis.steer((1.5 - dir) * 60);
        while (irSensors.getDistance(1) < 155) {
          gyro.updateGyro();
        }
      } else if (check2 > 1) {
        // If the robot needs to turn on the inside, go forward a bit and then turn
        chassis.steer(0);
        delay_2(400);
        chassis.steer((1.5 - dir) * 80);
        int prevTime = millis();

        while (abs(gyro.getAngle()) < (abs(targetAngle) - 30)) {
          if(irSensors.getFarDistance((dir == 1 ? 2: 0)) <= 18) break;
          gyro.updateGyro();
        }

      } else {  // If the robot sees nothing, turn
        chassis.steer((1.5 - dir) * 80);
        int prevTime = millis();
        // gyro.angle = 0;
        while (abs(gyro.getAngle()) < (abs(targetAngle) + 0) && ((camera.getClosestBlock().m_signature != 3 - dir && (irSensors.getFarDistance((dir == 1 ? 2: 0)) <= 18)) || abs(gyro.getAngle()) < (abs(targetAngle) - 40))) {
          gyro.updateGyro();
        }
        if (camera.getClosestBlock().m_signature > 2) {
          delay_2(100);
        }
      }
    }
    cornerScanDelay = millis();
  }
  if (irSensors.getFarDistance(0) <= 15) {
    steer = 20;
  } else if (irSensors.getFarDistance(2) <= 15) {
    steer = -20;
  }

  if (irSensors.getDistance(3)) {
    chassis.steer(0);
    chassis.move(-255);
    delay_2(3000);
    chassis.move(255);
    endTime += 2000;
    cornerScanDelay = millis();
  }

  if (steer>30){
    steer = 30;
  }else if (steer<-30){
    steer = -30;
  }

  gyro.updateGyro();

  if (millis() < endTime) {  // If the time is not finished, keep moving the robot
    chassis.steer(steer);
    chassis.move(speed);
  } else {  // If the time is up, stop the robot
    chassis.move(0);
    chassis.steer(0);
    delay(10000000);
  }
}

void loop() {
  // open();
  obstacle();
  // gyroTest();
}

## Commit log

2023-07-12 Updates on models
    [Battery Mount.stl, Servo Adapter.stl]
2023-07-14 Changed README.md and added Motor Test.py
2023-07-15 Added CAD Files
    [Motor Adapter.stl, Raspberry Pi Mount.stl, Servo Mount.stl]
2023-07-22 Updates to Code, Electrical, and Models
    [Battery Mount.stl, Motor Mount.stl, Raspberry Pi Mount.stl]
2023-07-22 Added Motor Mount Image
2023-07-29 Added Schematic and Changed Open Code
2023-08-11 Added models
    [Battery Mount.stl, Gear.stl, Motor Adapter.stl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]
2023-08-11 Updated CAD Models
2023-08-12 Motor mounts/bracket update
2023-08-14 Updated Schematic
2023-08-22 Added Schematic
2023-08-23 New IR Sensor Update
